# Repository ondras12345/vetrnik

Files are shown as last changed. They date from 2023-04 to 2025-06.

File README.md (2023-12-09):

# vetrnik
Power electronics for heating water using power generated by a small wind
turbine.

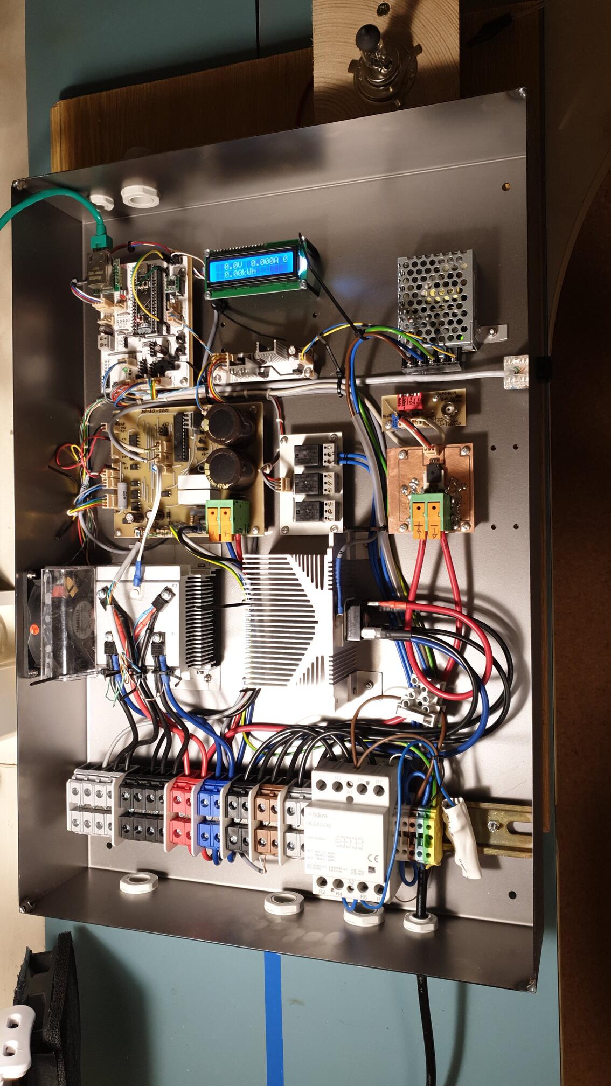
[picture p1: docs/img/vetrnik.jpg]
A photograph of the enclosure containing the wind turbine control electronics


## Features / design goals
- No battery.
- Maximum power point tracking.
- Power to resistive heating elements is AC to prevent electrolytic corrosion.
- MQTT telemetry.
- Home Assistant integration via MQTT.
- Energy meter.
- Calculates RPM from wind turbine AC output frequency.
- Survives full 50 V / 40 A during normal operation, as well as significantly
  higher open-circuit voltage.

The device offers a feature-rich command line interface:
```
vetrnik-control:$ help
---- Available commands ----

SPIflash: Issue commands to SPI flash
conf: Get or set configuration options.
control: Get or set params of control algorithm.
debug: Filter debug messages
dfu: Switch to DFU firmware download mode.
ds18b20: Print out DS18B20 sensor readings
free: Print out amount of free memory.
ifconfig: Print out networking information.
lisp: Process a line of Lisp
lisp_read: Execute Lisp from file
lisp_reset: Reinit Lisp interpreter
log: Print log / postmort
millis: Returns the number of milliseconds passed since the program started.
mqtt: Print out MQTT status.
onewirescan: Scan devices on onewire bus
ota: Switch to over-the-air firmware dl mode.
power: Print status of power PCB or set params.
pump: Control circulation pump.
reset: Reset the MCU.
rx: Print out RX_datapoints.
rx_raw: Toggle printing of messages from power board.
stats: Get stats (energy, ...)
tx: Set value of TX datapoint.
tx_raw: Transmit message to power board.
uptime: Returns the time passed since the program started.
ver: Print out version info.
watch: Run command every second.

vetrnik-control:$ stats
stats:
energy: 0.000 kWh

vetrnik-control:$ power
power board status:
retrieved_millis: 2274816315
valid: 1
time: 56810 s
mode: 2
duty: 0 (0-255)
OCP_max_duty: 255 (0-255)
RPM: 0 RPM
voltage: 0.0 V
current: 0.000 A
enabled.hardware: 1
enabled.software: 1
enabled.overall: 1
emergency: 0
temperature_heatsink: 16.3 'C
temperature_rectifier: 16.4 'C
fan: 0
error_count: 0
last5m: 0

vetrnik-control:$ ds18b20
This command does NOT request a new conversion.
[0] voda: 28.93 C
[1] : 0.00 C
[2] : 0.00 C
[3] : 0.00 C
[4] : 0.00 C
[5] : 0.00 C
[6] : 0.00 C
[7] : 0.00 C
[8] : 0.00 C
[9] : 0.00 C

vetrnik-control:$ SPIflash -h
Usage: SPIflash [erase_chip|ls | create name length erasable | rm name
   | dump name start | dumpchip start | erase filename | ed filename start]

vetrnik-control:$ SPIflash ls
Files:
address (HEX)	name	size (Bytes)
010000	settings	65536
020000	init.lisp	65536

vetrnik-control:$ lisp (= test (/ (+ 1 3) 2))
nil
Success: 1

vetrnik-control:$ lisp test
2
Success: 1

vetrnik-control:$ log
Usage: log (all|new)

vetrnik-control:$ log all
Printing whole log...
---
[      0] event: 0x0D log reinit
[      0] boot: 0x05 POWER-ON_RESET (POR) / POWER-DOWN_RESET (PDR)
[      0] event: 0x00 Eth begin
[      5] event: 0x01 Eth got IP
[      5] control strategy: old=control_shorted new=control_shorted
[      5] MQTT state: -1 DISCONNECTED
[     20] event: 0x03 MQTT connected
[     21] MQTT state: 0 CONNECTED
[   6315] control strategy: old=control_shorted new=control_lisp
[  82610] event: 0x10 DS18B20 error
[ 966931] MQTT state: -3 CONNECTION_LOST
[ 966932] event: 0x03 MQTT connected
[ 966932] MQTT state: 0 CONNECTED
[3386627] MQTT state: -2 CONNECT_FAILED
[3386810] event: 0x03 MQTT connected
[3386810] MQTT state: 0 CONNECTED
[3386870] event: 0x03 MQTT connected
[3387652] MQTT state: -3 CONNECTION_LOST
[3387652] event: 0x03 MQTT connected
[3387652] MQTT state: 0 CONNECTED
[3387712] event: 0x03 MQTT connected
[3387772] MQTT state: -3 CONNECTION_LOST
[3387772] event: 0x03 MQTT connected
[3387772] MQTT state: 0 CONNECTED
[3387814] control strategy: old=control_lisp new=control_shorted
[      0] boot: 0x04 SOFTWARE_RESET
[      0] event: 0x00 Eth begin
[      5] event: 0x01 Eth got IP
[      5] control strategy: old=control_shorted new=control_shorted
[      5] MQTT state: -1 DISCONNECTED
[     20] event: 0x03 MQTT connected
[     20] MQTT state: 0 CONNECTED
[     28] MQTT receive: length=1
[     29] MQTT receive: length=11
[     29] control strategy: old=control_shorted new=control_lisp
[ 118759] MQTT state: -3 CONNECTION_LOST
[ 118760] event: 0x03 MQTT connected
[ 118760] MQTT state: 0 CONNECTED
[ 721373] MQTT state: -3 CONNECTION_LOST
[ 721373] MQTT state: -2 CONNECT_FAILED
[ 721414] event: 0x03 MQTT connected
[ 721414] MQTT state: 0 CONNECTED
[ 982793] MQTT state: -3 CONNECTION_LOST
[ 982794] event: 0x03 MQTT connected
[ 982794] MQTT state: 0 CONNECTED
[ 983379] MQTT state: -3 CONNECTION_LOST
[ 983380] event: 0x03 MQTT connected
[ 983380] MQTT state: 0 CONNECTED
[2274043] MQTT receive: length=1
[2274062] MQTT receive: length=1
done

vetrnik-control:$
```

## Hardware details
See [`hardware/`](hardware/).

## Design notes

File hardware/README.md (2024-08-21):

# Vetrnik hardware
Block diagram:
```
            3 phase
+---------+ contactor +-----------+ DC +--------+ +-----------+ 1-phase +---------+
| Turbine +-+__/ __---+ rectifier +-+--+ ACS770 +-+ H-bridge  +---------+ heater  +
+---------+ |  ^      +-----------+ |  +----+---+ +-----------+ AC      +---------+
            |  |                    |       |          ^
            |  |             voltage|       |          |
            |  |                    |       | current  | duty
            |  |                    v       |          |
  frequency |  |      +-------------+-+     |          |
  (RPM)     |  +------+ vetrnik-power +<----+          |
            +-------->+               +----------------+
                      +-------+-------+
                              ^
                              | UART
                              v
                      +-------+-----------+
                      |  vetrnik-control  |
                      |                   +<----------> Ethernet
                      +-------------------+
```

The hardware consists of several PCBs in a custom-made enclosure. Most PCBs
are single-sided and designed to be milled out on a CNC.
- vetrnik-power
  - Controlled by an ATmega8 MCU.
  - Controls a FET H-bridge mounted on a heatsink.
  - Has isolated power supply, its GNDPWR is at wind turbine output potential.
  - Receives commands from vetrnik-control via optically isolated UART.
  - No remote firmware updates, no bootloader.
  - This PCB also contains analog comparator-based emergency stop circuitry
    that handles over-voltage condition even if the MCU is not working.
- vetrnik-control
  - Controlled by STM32F401.
  - Handles smart features (Ethernet, telnet, MQTT).
  - Implements LISP-like interpreted language that can be used to send
    commands to vetrnik-power. MPPT controller is implemented on this device
    in LISP.
  - Supports OTA firmware updates.
- vetrnik-current-sensor
  - A double-sided PCB with heavy copper. It passes all the current from the
    bridge rectifier through an ACS770-050U hall-effect current sensor.
- vetrnik-current-sensor-opamp
  - This PCB contains some additional signal-conditioning circuitry to improve
    current sensing precision and filter out noise.
- vetrnik-power-supply
  - A power supply board that converts 12 V from MeanWell power supply to
    various voltage levels needed by the device.
    The 3.3V voltage regulator is switch mode, 5V regulator is linear.
- vetrnik-relays
  - This is just a simple board with 3 relays that can be used to switch 230V
    devices like the coil of the contactor used to disconnect the wind turbine
    output, and a circulator pump.

## Wind turbine
- iSta breeze i-2000 Windsafe
- three phase
- 2 kW nominal power, 2.2 kW max
- 6 pole pairs --> 10 RPM / Hz

## Load
- 4x 600 W resistive heating element
- https://www.growzone.cz/48V-1200W-topna-patrona-G-6-4-palce-38x-197mm-d8275.htm

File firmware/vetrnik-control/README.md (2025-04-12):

# vetrnik-control
Firmware for STM32F4. Handles telemetry and remote control via MQTT,
MPPT controller, etc.

## Architecture
```text
        +-------+   +-------+     +----------+   cmnd_tx_raw
        | LISP  |   | MQTT  |     | CLI      +-----------------+
        +---+---+   +---+-+-+     +-----+--+-+                 |
            |           | |             |  | cmnd_tx           |
      +-----|-----------|-+-------------|--+                   |
RX_   |     |           |               |                      |
data  | +---+-----------+---------------+---------------+      |
points| |               wt_hal / hal.c                  |      |
_get()| +--------+----------------------+---------+-----+      |
  /   |          |                      |         |            |
TX_   | +--------+----------+     +-----+-----+   |            |
data  | | power_board       |     | control   |   |            |
points| +--------+----------+     +-----------+   |            |
_set()|==========|================================|============|===============
    +-+----------+--------+                       |            |
    | power_datapoints    |                       |            |
    +------------+--------+                       |            |
                 |                                |            |
        +--------+----+                   +-------+-----+      |     HARDWARE
        | uart_power  |                   | sensor_wind |      |      DRIVERS
        +--------+----+                   +-------+-----+      |
                 |                                |            |
                 +<-------------------------------|------------+
                 | UART                           |
=================|================================|============================
                 |                                |                 HARDWARE
    +------------+--------+       +---------------+-----+
    | vetrnik-power PCB   |       | wind sensor (RS485) |
    +---------------------+       +---------------------+
```

## Lisp-like REPL
A Lisp-like interpreted language called [fe](https://github.com/rxi/fe) is
included. It can be used by calling the `lisp` CLI command or via MQTT.

The intention is that the user can write a custom control algorithm and have
it run directly on the device without updating its firmware.

See [`lisp/spec.md`](lisp/spec.md).

### MISC Lisp code
Test OOM:
```lisp
(= a 0)
(while t
  (= l (cons a l))
  (= a (+ a 1))
)
```
On PC: a = 1852, does not get completely stuck (can still create new numeric
variables)
On STM (8*1024 bytes): a = 329

Patch for testing in lab without DS18B20 sensors:
```lisp
(= ds18 (fn () 23.4))
```

## Telnet
To connect with telnet on GNU/Linux, use this command:
```sh
# netcat - better
stty -icanon -echo && nc -NC -O 1 192.168.1.188 23

# telnet - sends garbage at startup
telnet 192.168.1.188 23  # specifying the port should disable negotiation
```

It is recommended to put the following configuration in your `~/.telnetrc` if
you want to use the `telnet` command:
```
# vetrnik-control
192.168.1.188
    mode character
    # TODO improve
```

## Build
Just run `make` in this directory. GNU/Linux OS with PlatformIO installed is
required.
Type `make help` for more info.

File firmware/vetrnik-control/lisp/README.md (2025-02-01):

# Lisp
This directory contains the lisp code for vetrnik-control.

Type `make` to compile `out.lisp`, which is the file to be written to the SPI
flash.

This directory also contains [documentation for the lisp
environment](spec.md) (automatically generated from `spec.yaml` by
`make`).

## Uploading
Simple:
```
# connect via telnet (do not use that nc trick, it does not work)
erase init.lisp
hexdump init.lisp 0
ed init.lisp 0
# paste out.lisp
.
reset
```

Advanced:
```
filltext init.lisp
# will print end address
ed init.lisp $end_addr+1
# paste out.lisp
.
reset
# (or lisp_reset & lisp_read with addr)
```

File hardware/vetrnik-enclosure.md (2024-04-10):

# Vetrnik enclosure
## Cable feed-throughs
- 230V IN: OD 7mm, GPA-M16
- wind turbine IN: EG-13.5GY (drill 20,4mm)
- heater OUT: EG-13.5GY (drill 20,4mm) + EG-13.5GY (90mm from left edge)
- ethernet UTP: EG-7BL (drill 12,5mm)
- USB-C: EG-13.5GY (drill 20,4mm) (combine with mechanical thermostat, temp sensors)
- temperature sensors: RJ45 KEJ-C5E-U-BK 20x15mm
- dump load?: EG-13.5GY (drill 20,4mm)
- 230V pump: GPA-M16 (50mm from right edge)

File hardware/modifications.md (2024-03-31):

- See `heater-elements.ipynb`.
- 2023-12-24 10:17 jsme zjistili, ze odesly Q2, Q4 v H-mustku (zkrat)
  - Q3 odpojen cerveny vodic
  - Q2 odpojen cerny vodic
  - melo by to fungovat jako half-bridge
  - Q2, Q4 piskala kontinuita cerny vodic proti modre svorkovnici
  - myslim, ze tranzistory odesly okolo 2023-12-22 22:00
    - Tocila se vrtule a ja se ji snazil rucne zastavit. Pri startu do male
      stridy se resetovala vykonova elektronika. Dal jsem vic (asi 50?),
      vrtule se zastavila.
    - Ale vubec to tim byt nemusi, protoze hned potom jsem navysil
      RL z 80 na 200?, takze proto od te doby tekly vetsi proudy.
  - Mohly umrit na prepeti (vrtule se volne tocila >1000 RPM >160V, v noci
    predtim dokonce nemerena (vypadlo 230V).
  - Nebo mohly umrit na to, ze byla spatne zapojena zatez (4 smycky
    paralelne), ale to bylo porad mnohem vic nez Rds on.

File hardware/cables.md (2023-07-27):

# Cables
## DS18B20 temperature sensors
- RJ45:

| pin | color | function | DS18B20 pin |
|:-----:|:---:|:---|:---:|
| 1 | orange/white  | | |
| 2 | orange | +5V | 3 |
| 3 | green/white | | |
| 4 | blue | 1-wire data | 2 |
| 5 | blue/white | GND | 1 |
| 6 | green | | |
| 7 | brown/white | | |
| 8 | brown | | |

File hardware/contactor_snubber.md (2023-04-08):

# Contactor RC snubber
Ethernet module would reset when contactor was operating (both on and off).
With a x100 oscilloscope probe, I was able to detect 1.5kV peak from one relay
contact to PE when the contactor was switching off. With the RC snubber in
parallel with relay contacts, the contactor would never switch off after being
operated once due to current flowing through the capacitor. RC snubber in
parallel with contactor's coil would reduce the peak voltage to <700V.
However, it wouldn't prevent the Ethernet module from resetting. I had to add
a 10nF capacitor to the module's RSTn pin for that.

There is some info about RC snubber desing in `contactor_snubber.m`.
However, I decided to use the generic laskakit.cz snubber (100 nF, 220 ohm and
a MOV). I'll likely need to put a fuse in series to protect from MOV failure.

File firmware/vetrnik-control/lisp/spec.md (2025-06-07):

# Language
See [fe language overview](https://github.com/rxi/fe/blob/master/doc/lang.md)
for more information about the language and built-in functions.

# Types
- number: a floating-point number
- string: a sequence of characters
- nil: always `nil`
- bool: either `nil` (false), or any other value (true)
- any: placeholder used in this document to indicate values of
  more than one type are acceptable.

# Categories
- LCD: functions that control the display
- callbacks: functions to be implemented by the user to respond to various events

# Custom functions
## `rem`
### Description
Perform the operation truncate on number and divisor and return the
remainder of the truncate operation.

https://stackoverflow.com/questions/5706398/how-to-get-the-modulus-in-lisp

### Signature
```lisp
(rem
    number
    divisor
)
```

### Arguments
- `number` \[number\]
- `divisor` \[number\]

### Return value
\[number\]: `(int)x % (int)y`

### Example
```lisp
(rem 3 2) ; 1
(rem -3 2) ; -1
```

## `round`
### Description
Return the closest integer to x, rounding to even when x is halfway between two integers.

### Signature
```lisp
(round
    x
)
```

### Arguments
- `x` \[number\]: number to round

### Return value
\[number\]

### Example
```lisp
(round 0.4999) ; 0
(round 0.5) ; 0
(round 0.5001) ; 1

(round 1.4999) ; 1
(round 1.5) ; 2
(round 1.5001) ; 2
```

## `map`
### Description
Linearly map a value from one range to another.

This could be easily implemented in Lisp, but a cfunc takes up less
memory.
Equivalent lisp implementation:
```lisp
(= map (fn (v fl fh tl th)
  (+ tl
     (/ (* (- v fl)
           (- th tl))
        (- fh fl)))))
```

### Signature
```lisp
(map
    value
    from_low
    from_high
    to_low
    to_high
)
```

### Arguments
- `value` \[number\]: the number to map
- `from_low` \[number\]: lower bound of `value`'s current range
- `from_high` \[number\]: upper bound of `value`'s current range
- `to_low` \[number\]: lower bound of `value`'s target range
- `to_high` \[number\]: upper bound of `value`'s target range

### Return value
\[number\]: `value` remapped to the target range

### Example
```lisp
(map 10 0 100 0 1) ; 0.1
(map 10 0 100 -1 0) ; -0.9
```

## `lim`
### Description
Limit a number to a range.

Equivalent lisp implementation:
```lisp
(= lim (fn (x l h)
  (if
    (< x l) l
    (< h x) h
    x)))
```

### Signature
```lisp
(lim
    x
    low
    high
)
```

### Arguments
- `x` \[number\]: value to be processed
- `low` \[number\]: lower bound for the value's range
- `high` \[number\]: upper bound for the value's range

### Return value
\[number\]
## `pow`
### Description
Compute x raised to the power of y.

### Signature
```lisp
(pow
    x
    y
)
```

### Arguments
- `x` \[number\]
- `y` \[number\]

### Return value
\[number\]
## `pwrg`
### Description
Get a value from the power board state object. Numerical values (in SI units without metric prefix) are returned.

### Signature
```lisp
(pwrg
    name
    [relay_nr]
)
```

### Arguments
- `name` \[string\]
    - `"valid"`
    - `"time"`
    - `"mode"`
    - `"duty"`
    - `"OCP_max_duty"`
    - `"RPM"`
    - `"voltage"`
    - `"current"`
    - `"hw_enable"`
    - `"sw_enable"`
    - `"enabled"`
    - `"emergency"`
- `relay_nr` \[number\]: relay number (starting from 1); only used if name == "REL"

### Return value
\[any\]
## `pwrs`
### Description
Set parameters on the power board.

Variables are added for the constants from `power_board_mode_t` enum.
They are prefixed with `pwr_`, e.g. `pwr_start`.

### Signature
```lisp
(pwrs
    name
    value
    ...
)
```

### Arguments
- `name` \[string\]
    - `"duty"`
    - `"mode"`
    - `"REL"`
    - `"sw_enable"`
- `value` \[any\]: Desired value (expected type depends on 'name')

### Return value
\[nil\]
## `lcdc`
Category: LCD

### Description
Set LCD cursor position to specified column.

### Signature
```lisp
(lcdc
    column
)
```

### Arguments
- `column` \[number\]

### Return value
\[nil\]
## `lcdw`
Category: LCD

### Description
Write LCD buffer to specified line (row).

### Signature
```lisp
(lcdw
    row
)
```

### Arguments
- `row` \[number\]

### Return value
\[nil\]
## `lcds`
Category: LCD

### Description
Print a string to the LCD buffer.

### Signature
```lisp
(lcds
    str
)
```

### Arguments
- `str` \[string\]

### Return value
\[nil\]
## `lcdn`
Category: LCD

### Description
Print a number to the LCD buffer.

### Signature
```lisp
(lcdn
    number
    align
    precision
)
```

### Arguments
- `number` \[number\]: number to print
- `align` \[number\]: (integer) TODO
- `precision` \[any\]: (integer) number of decimal places (TODO verify)

### Return value
\[nil\]
## `lcdb`
Category: LCD

### Description
Get or set LCD backlight status.

### Signature
```lisp
(lcdb
    [state]
)
```

### Arguments
- `state` \[bool\]: Desired backlight status

### Return value
\[bool\]: LCD backlight status
## `stats`
### Description
Get a value from the stats struct.

### Signature
```lisp
(stats
    name
)
```

### Arguments
- `name` \[string\]
    - `"energy"`

### Return value
\[number\]: value
## `ctrlg`
### Description
Get a value from the control subsystem.

### Signature
```lisp
(ctrlg
    name
)
```

### Arguments
- `name` \[string\]
    - `"strategy"`
    - `"contactor"`
    - `"vwind"`

### Return value
\[any\]
## `ctrls`
### Description
Set a value in the control subsystem.

### Signature
```lisp
(ctrls
    name
    value
)
```

### Arguments
- `name` \[string\]
    - `"strategy"`
    - `"contactor"`
- `value` \[any\]: Desired value (expected type depends on 'name')

### Return value
\[nil\]
## `out`
### Description
Get or set state of digital outputs (LEDs and relays) on the control board.

### Signature
```lisp
(out
    out_id
    [state]
)
```

### Arguments
- `out_id` \[string\]
    - `"LED_BLUE"`
    - `"LED_RED"`
    - `"PUMP"`
    - `"REL2"`
- `state` \[bool\]: desired state

### Return value
\[bool\]: state of the digital output
## `ds18`
### Description
Read temperature from DS18B20 sensors.

### Signature
```lisp
(ds18
    sensor_number
)
```

### Arguments
- `sensor_number` \[number\]

### Return value
\[number\]: temperature in degrees C. nil is returned if sensor is broken.
## `ctrl`
Category: callbacks

### Description
If set up for `LISP` control strategy, the device will call this function
each time a new state object is received.
This function is empty by default, the user is expected to overwrite it
with their own implementation.

### Signature
```lisp
(ctrl
)
```

### Arguments

### Return value
\[nil\]

### Example
```lisp
;;; A simple "blink" control function:
(= dl 50) ; off state duty
(= dh 200) ; on state duty
(= p 5) ; period in seconds
(= pt 0) ; prev time
(= ctrl (fn ()
  ; t is used for "true", do not overwrite - named ti instead
  (let ti (pwrg "time"))
  ; max time is 65535 (see power report()), so no problem with rem
  (if (and (is (rem ti p) 0) (not (is ti pt)))
    (do
      (= pt ti)
      (pwrs "duty" (if (<= (pwrg "duty") dl) dh dl))
    )
  )
))

;;; Simple RPM threshold-based control:
(= ctrl (fn ()
  (let r (pwrg "RPM")) ; current RPM
  (pwrs "duty"
    (if
      ; pretty much random values
      (< r 10) 0
      (< r 15) 10
      (< r 20) 20
      (< r 30) 40
      (< r 60) 100
      255
    )
  )
))
```

## `disp`
Category: callbacks

### Description
The `disp` function is executed every 0.5 s. It is meant to be used to
control the display.
This function is empty by default, the user is expected to overwrite it
with their own implementation.

### Signature
```lisp
(disp
)
```

### Arguments

### Return value
\[nil\]
## `btn1_short`
Category: callbacks

### Description
Called when button 1 is released after a short press.

### Signature
```lisp
(btn1_short
)
```

### Arguments

### Return value
\[nil\]
## `btn1_long`
Category: callbacks

### Description
Called when button 1 is released after a long press.

### Signature
```lisp
(btn1_long
)
```

### Arguments

### Return value
\[nil\]
## `btn2_short`
Category: callbacks

### Description
Called when button 2 is released after a short press.

### Signature
```lisp
(btn2_short
)
```

### Arguments

### Return value
\[nil\]
## `btn2_long`
Category: callbacks

### Description
Called when button 2 is released after a long press.

### Signature
```lisp
(btn2_long
)
```

### Arguments

### Return value
\[nil\]

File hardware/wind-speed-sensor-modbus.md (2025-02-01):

# Wind speed sensor modbus
- RS-FSJT-N01

## Initial testing
- 12 V power brown +, black -
- yellow (green) RS-485 A, blue: RS-485 B
- PL2303-485 USB converter (PL-2303HX + MAX485ESA)

```console
$ sudo apt install mbpoll

$ mbpoll -m rtu -a 1 -t 3 -r 1 -c 1 -l 500 -b 4800 /dev/ttyUSB0
# does not work

# debug:
$ mbpoll -v -m rtu -a 1 -t 3 -r 1 -c 1 -l 500 -b 4800 /dev/ttyUSB0
debug enabled
Set mode=rtu
iGetIntList(1)
Integer found: 1
iCount=1
Set function=3
Set start reference=1
Set number of values=1
Set poll rate=500
Set rtu baudrate=4800
Set device=/dev/ttyUSB0
mbpoll 1.0-0 - FieldTalk(tm) Modbus(R) Master Simulator
Copyright © 2015-2019 Pascal JEAN, https://github.com/epsilonrt/mbpoll
This program comes with ABSOLUTELY NO WARRANTY.
This is free software, and you are welcome to redistribute it
under certain conditions; type 'mbpoll -w' for details.

Opening /dev/ttyUSB0 at 4800 bauds (E, 8, 1)
Set response timeout to 1 sec, 0 us
Protocol configuration: Modbus RTU
Slave configuration...: address = [1]
                        start reference = 1, count = 1
Communication.........: /dev/ttyUSB0,       4800-8E1 
                        t/o 1.00 s, poll rate 500 ms
Data type.............: 16-bit register, input register table

-- Polling slave 1... Ctrl-C to stop)
[01][04][00][00][00][01][31][CA]
Waiting for a confirmation...
<01><00><00><00><00>
ERROR CRC received 0x0 != CRC calculated 0x2000
Read input register failed: Invalid CRC
-- Polling slave 1... Ctrl-C to stop)
[01][04][00][00][00][01][31][CA]
Waiting for a confirmation...
<01><00><00><00><00>
ERROR CRC received 0x0 != CRC calculated 0x2000
Read input register failed: Invalid CRC
-- Polling slave 1... Ctrl-C to stop)
[01][04][00][00][00][01][31][CA]
Waiting for a confirmation...
<01><00><00><00><FE>
ERROR CRC received 0xFE != CRC calculated 0x2000
Read input register failed: Invalid CRC
-- Polling slave 1... Ctrl-C to stop)
[01][04][00][00][00][01][31][CA]
Waiting for a confirmation...
<01><00><00><00><FE>
ERROR CRC received 0xFE != CRC calculated 0x2000
Read input register failed: Invalid CRC
```

According to the manual, only modbus function code 0x03 (read register data)
is supported.

```console
$ mbpoll -v -m rtu -a 1 -t 4 -r 1 -c 1 -l 500 -b 4800 /dev/ttyUSB0
debug enabled
Set mode=rtu
iGetIntList(1)
Integer found: 1
iCount=1
Set function=4
Set start reference=1
Set number of values=1
Set poll rate=500
Set rtu baudrate=4800
Set device=/dev/ttyUSB0
mbpoll 1.0-0 - FieldTalk(tm) Modbus(R) Master Simulator
Copyright © 2015-2019 Pascal JEAN, https://github.com/epsilonrt/mbpoll
This program comes with ABSOLUTELY NO WARRANTY.
This is free software, and you are welcome to redistribute it
under certain conditions; type 'mbpoll -w' for details.

Opening /dev/ttyUSB0 at 4800 bauds (E, 8, 1)
Set response timeout to 1 sec, 0 us
Protocol configuration: Modbus RTU
Slave configuration...: address = [1]
                        start reference = 1, count = 1
Communication.........: /dev/ttyUSB0,       4800-8E1 
                        t/o 1.00 s, poll rate 500 ms
Data type.............: 16-bit register, output (holding) register table

-- Polling slave 1... Ctrl-C to stop)
[01][03][00][00][00][01][84][0A]
Waiting for a confirmation...
<01><00><00><B8><00>
ERROR CRC received 0xB800 != CRC calculated 0x2000
Read output (holding) register failed: Invalid CRC
-- Polling slave 1... Ctrl-C to stop)
[01][03][00][00][00][01][84][0A]
Waiting for a confirmation...
<01><00><00><00><00>
ERROR CRC received 0x0 != CRC calculated 0x2000
Read output (holding) register failed: Invalid CRC
-- Polling slave 1... Ctrl-C to stop)
[01][03][00][00][00][01][84][0A]
Waiting for a confirmation...
<01><00><00><00><00>
ERROR CRC received 0x0 != CRC calculated 0x2000
Read output (holding) register failed: Invalid CRC
^C--- /dev/ttyUSB0 poll statistics ---
3 frames transmitted, 0 received, 3 errors, 100.0% frame loss

everything was closed.
Have a nice day !
```

Now the query matches the manual, but there still is no response.

Connected grounds together.

I can see responses on the oscilloscope, but mbpoll still complains:
```console
$ mbpoll -v -m rtu -a 1 -t 4 -r 1 -c 1 -l 500 -b 4800 /dev/ttyUSB0
debug enabled
Set mode=rtu
iGetIntList(1)
Integer found: 1
iCount=1
Set function=4
Set start reference=1
Set number of values=1
Set poll rate=500
Set rtu baudrate=4800
Set device=/dev/ttyUSB0
mbpoll 1.0-0 - FieldTalk(tm) Modbus(R) Master Simulator
Copyright © 2015-2019 Pascal JEAN, https://github.com/epsilonrt/mbpoll
This program comes with ABSOLUTELY NO WARRANTY.
This is free software, and you are welcome to redistribute it
under certain conditions; type 'mbpoll -w' for details.

Opening /dev/ttyUSB0 at 4800 bauds (E, 8, 1)
Set response timeout to 1 sec, 0 us
Protocol configuration: Modbus RTU
Slave configuration...: address = [1]
                        start reference = 1, count = 1
Communication.........: /dev/ttyUSB0,       4800-8E1 
                        t/o 1.00 s, poll rate 500 ms
Data type.............: 16-bit register, output (holding) register table

-- Polling slave 1... Ctrl-C to stop)
[01][03][00][00][00][01][84][0A]
Waiting for a confirmation...
<01><00><00><00><00>
ERROR CRC received 0x0 != CRC calculated 0x2000
Read output (holding) register failed: Invalid CRC
-- Polling slave 1... Ctrl-C to stop)
[01][03][00][00][00][01][84][0A]
Waiting for a confirmation...
<01><00><00><00><00>
ERROR CRC received 0x0 != CRC calculated 0x2000
Read output (holding) register failed: Invalid CRC
-- Polling slave 1... Ctrl-C to stop)
[01][03][00][00][00][01][84][0A]
Waiting for a confirmation...
<01><00><00><00><00>
ERROR CRC received 0x0 != CRC calculated 0x2000
Read output (holding) register failed: Invalid CRC
^C--- /dev/ttyUSB0 poll statistics ---
3 frames transmitted, 0 received, 3 errors, 100.0% frame loss

everything was closed.
Have a nice day !
```

Parity was not set properly.
```console
$ mbpoll -m rtu -a 1 -t 4 -r 1 -c 1 -l 500 -b 4800 -P none /dev/ttyUSB0
mbpoll 1.0-0 - FieldTalk(tm) Modbus(R) Master Simulator
Copyright © 2015-2019 Pascal JEAN, https://github.com/epsilonrt/mbpoll
This program comes with ABSOLUTELY NO WARRANTY.
This is free software, and you are welcome to redistribute it
under certain conditions; type 'mbpoll -w' for details.

Protocol configuration: Modbus RTU
Slave configuration...: address = [1]
                        start reference = 1, count = 1
Communication.........: /dev/ttyUSB0,       4800-8N1 
                        t/o 1.00 s, poll rate 500 ms
Data type.............: 16-bit register, output (holding) register table

-- Polling slave 1... Ctrl-C to stop)
[1]: 	0
-- Polling slave 1... Ctrl-C to stop)
[1]: 	0
-- Polling slave 1... Ctrl-C to stop)
[1]: 	0
-- Polling slave 1... Ctrl-C to stop)
[1]: 	0
-- Polling slave 1... Ctrl-C to stop)
[1]: 	0
-- Polling slave 1... Ctrl-C to stop)
[1]: 	0
-- Polling slave 1... Ctrl-C to stop)
[1]: 	0
-- Polling slave 1... Ctrl-C to stop)
[1]: 	0
-- Polling slave 1... Ctrl-C to stop)
[1]: 	11
-- Polling slave 1... Ctrl-C to stop)
[1]: 	14
-- Polling slave 1... Ctrl-C to stop)
[1]: 	14
-- Polling slave 1... Ctrl-C to stop)
[1]: 	11
-- Polling slave 1... Ctrl-C to stop)
[1]: 	11
-- Polling slave 1... Ctrl-C to stop)
[1]: 	8
-- Polling slave 1... Ctrl-C to stop)
[1]: 	8
-- Polling slave 1... Ctrl-C to stop)
[1]: 	6
-- Polling slave 1... Ctrl-C to stop)
[1]: 	6
-- Polling slave 1... Ctrl-C to stop)
[1]: 	4
-- Polling slave 1... Ctrl-C to stop)
[1]: 	4
-- Polling slave 1... Ctrl-C to stop)
[1]: 	2
-- Polling slave 1... Ctrl-C to stop)
[1]: 	2
-- Polling slave 1... Ctrl-C to stop)
[1]: 	2
-- Polling slave 1... Ctrl-C to stop)
[1]: 	1
-- Polling slave 1... Ctrl-C to stop)
[1]: 	1
-- Polling slave 1... Ctrl-C to stop)
[1]: 	1
-- Polling slave 1... Ctrl-C to stop)
[1]: 	1
-- Polling slave 1... Ctrl-C to stop)
[1]: 	0
-- Polling slave 1... Ctrl-C to stop)
[1]: 	0
-- Polling slave 1... Ctrl-C to stop)
[1]: 	0
^C--- /dev/ttyUSB0 poll statistics ---
29 frames transmitted, 29 received, 0 errors, 0.0% frame loss

everything was closed.
Have a nice day !
```

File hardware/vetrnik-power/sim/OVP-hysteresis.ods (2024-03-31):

R1 | R2 | Vin | Vout |  |  | Vcc | R25 | R26 | R29 | R30 | Vh | Vl | Vhh nominal | 1,1*Vh | Vhh +10% | Vhh – 5% | Vll – 5%
1,00E+05 | 3,30E+03 | 178,5 | 5,702 |  | puvodni | 12 | 47,00E+03 | 22,00E+03 | 47,00E+03 | 3,30E+03 | 5,702 | 2,901 | 178,500 | 6,273 | 196,3 | 169,6 | 86,3
1,00E+05 | 3,30E+03 | 90,8 | 2,901 |  |  | 12 | 68,00E+03 | 18,00E+03 | 100,00E+03 | 3,30E+03 | 3,661 | 2,199 | 114,588 | 4,027 | 126,0 | 108,9 | 65,4
1,00E+05 | 3,30E+03 | 128 | 4,089 | x |  | 12 | 47,00E+03 | 22,00E+03 | 220,00E+03 | 3,30E+03 | 4,340 | 3,582 | 135,859 | 4,774 | 149,4 | 129,1 | 106,5
1,00E+05 | 3,30E+03 | 100 | 3,195 | x |  | 12 | 13,90E+03 | 5,60E+03 | 47,00E+03 | 3,30E+03 | 4,075 | 3,176 | 127,562 | 4,483 | 140,3 | 121,2 | 94,5
1,00E+05 | 3,30E+03 | 80 | 2,556 | x |  | 12 | 61,00E+03 | 19,80E+03 | 100,00E+03 | 3,30E+03 | 4,086 | 2,558 | 127,898 | 4,494 | 140,7 | 121,5 | 76,1
1,00E+05 | 3,30E+03 | 109 | 3,482 |  |  | 12 | 68,00E+03 | 22,00E+03 | 120,00E+03 | 3,30E+03 | 4,010 | 2,576 | 125,538 | 4,411 | 138,1 | 119,3 | 76,6
1,00E+05 | 3,30E+03 | 56 | 1,789 |  |  | 12 | 61,00E+03 | 17,00E+03 | 100,00E+03 | 3,30E+03 | 3,685 | 2,308 | 115,367 | 4,054 | 126,9 | 109,6 | 68,6
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

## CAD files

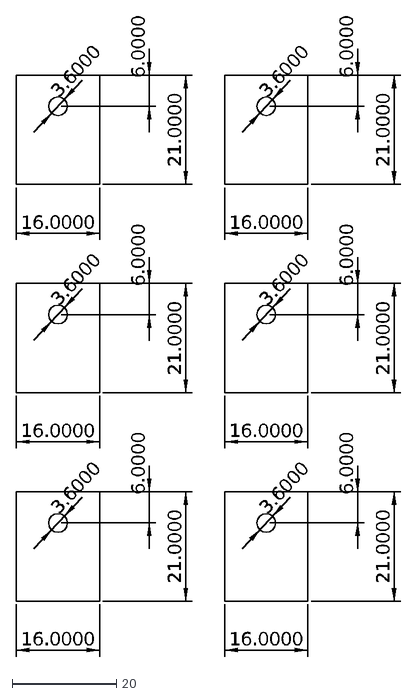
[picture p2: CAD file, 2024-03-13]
hardware/TO-247-scale.dxf
6.0000
21.0000
16.0000
3.6000

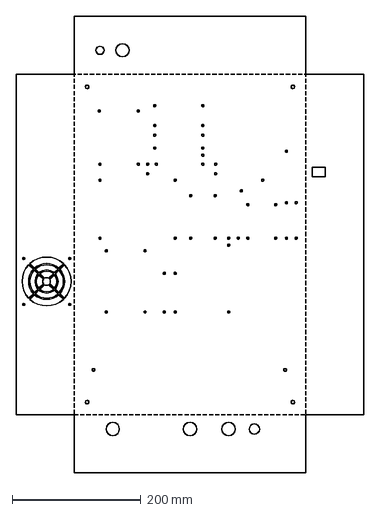
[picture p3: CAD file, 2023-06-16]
hardware/vetrnik-enclosure.dxf
540.0 x 710.0 mm

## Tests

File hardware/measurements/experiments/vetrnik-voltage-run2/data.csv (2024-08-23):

datetime | voltage_set | voltage_get1 | voltage_dmm1 | time1 | voltage_vetrnik1 | voltage_get2 | voltage_dmm2 | time2 | voltage_vetrnik2 | voltage_get3 | voltage_dmm3 | time3 | voltage_vetrnik3 | voltage_dmm1_V | voltage_dmm2_V | voltage_dmm3_V
2024-07-01 22:11:10.541995 | 2 | 2 | 02.342e00 V DC | 1354 | 2.1 | 2 | 02.369e00 V DC | 1355 | 2.1 | 2 | 02.383e00 V DC | 1357 | 2.1 | 2.342 | 2.369 | 2.383
2024-07-01 22:11:15.180022 | 3 | 3 | 03.930e00 V DC | 1359 | 3.6 | 3 | 03.957e00 V DC | 1360 | 3.8 | 3 | 03.967e00 V DC | 1361 | 3.8 | 3.93 | 3.957 | 3.967
2024-07-01 22:11:19.769974 | 5 | 5 | 07.140e00 V DC | 1363 | 6.8 | 5 | 07.156e00 V DC | 1365 | 7.0 | 5 | 07.158e00 V DC | 1366 | 7.0 | 7.14 | 7.156 | 7.158
2024-07-01 22:11:24.360379 | 10 | 10 | 014.39e00 V DC | 1368 | 14.2 | 11 | 014.39e00 V DC | 1369 | 14.2 | 11 | 014.40e00 V DC | 1370 | 14.2 | 14.39 | 14.39 | 14.4
2024-07-01 22:11:28.949898 | 15 | 16 | 022.47e00 V DC | 1373 | 22.2 | 16 | 022.50e00 V DC | 1374 | 22.2 | 16 | 022.51e00 V DC | 1375 | 22.4 | 22.47 | 22.5 | 22.51
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

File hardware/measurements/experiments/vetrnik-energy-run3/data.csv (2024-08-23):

datetime | time | energy_Ws_vetrnik | voltage_vetrnik | current_vetrnik | power_vetrnik | voltage_dmm | current_dmm | voltage_dmm_V | current_dmm_A | duration | power_dmm | energy_Ws_dmm
2024-07-04 16:54:33.008086 | 1192 | 0.0 | 10.3 | 0.0 | 0.0 | OVLOAD V DC | 00.000e00 A DC |  | 0.0 | 0.997626
2024-07-04 16:54:34.005712 | 1193 | 0.0 | 10.5 | 0.0 | 0.0 | OVLOAD V DC | 00.000e00 A DC |  | 0.0 | 0.999737
2024-07-04 16:54:35.005449 | 1194 | 0.0 | 10.5 | 0.0 | 0.0 | OVLOAD V DC | 00.000e00 A DC |  | 0.0 | 0.998184
2024-07-04 16:54:36.003633 | 1195 | 0.0 | 10.5 | 0.0 | 0.0 | 10.713e00 V DC | 00.000e00 A DC | 10.713 | 0.0 | 0.999894 | 0.0 | 0.0
2024-07-04 16:54:37.003527 | 1196 | 0.0 | 10.5 | 0.0 | 0.0 | 10.665e00 V DC | 00.000e00 A DC | 10.665 | 0.0 | 1.000543 | 0.0 | 0.0
2024-07-04 16:54:38.004070 | 1197 | 0.0 | 10.5 | 0.0 | 0.0 | 10.665e00 V DC | 00.000e00 A DC | 10.665 | 0.0 | 0.999808 | 0.0 | 0.0
2024-07-04 16:54:39.003878 | 1198 | 0.0 | 10.5 | 0.0 | 0.0 | 10.665e00 V DC | 00.000e00 A DC | 10.665 | 0.0 | 1.000897 | 0.0 | 0.0
2024-07-04 16:54:40.004775 | 1199 | 0.0 | 10.5 | 0.0 | 0.0 | 10.665e00 V DC | 00.000e00 A DC | 10.665 | 0.0 | 1.002683 | 0.0 | 0.0
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

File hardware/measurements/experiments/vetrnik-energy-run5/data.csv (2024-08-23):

datetime | time | energy_Ws_vetrnik | voltage_vetrnik | current_vetrnik | power_vetrnik | voltage_dmm | current_dmm | voltage_dmm_V | current_dmm_A | duration | power_dmm | energy_Ws_dmm
2024-07-04 17:24:34.873608 | 2994 | 4615.7 | 9.9 | 0.041 | 0.4 | OVLOAD V DC | 00.071e00 A DC |  | 0.071 | 1.12994
2024-07-04 17:24:36.003548 | 2995 | 4616.2 | 10.0 | 0.041 | 0.4 | OVLOAD V DC | 00.074e00 A DC |  | 0.074 | 1.000005
2024-07-04 17:24:37.003553 | 2996 | 4616.5 | 10.0 | 0.041 | 0.4 | OVLOAD V DC | 00.074e00 A DC |  | 0.074 | 1.002061
2024-07-04 17:24:38.005614 | 2997 | 4616.9 | 10.0 | 0.041 | 0.4 | 10.139e00 V DC | 00.074e00 A DC | 10.139 | 0.074 | 1.001461 | 0.7502859999999999 | 0.7513821678459999
2024-07-04 17:24:39.007075 | 2998 | 4618.8 | 9.9 | 0.205 | 2.0 | 10.270e00 V DC | 00.376e00 A DC | 10.27 | 0.376 | 1.000302 | 3.86152 | 4.614068346886
2024-07-04 17:24:40.007377 | 2999 | 4619.9 | 10.0 | 0.041 | 0.4 | 10.270e00 V DC | 00.076e00 A DC | 10.27 | 0.076 | 0.996426 | 0.78052 | 5.391798768406001
2024-07-04 17:24:41.003803 | 3000 | 4620.1 | 10.0 | 0.0 | 0.0 | 10.201e00 V DC | 00.057e00 A DC | 10.201 | 0.057 | 0.99991 | 0.581457 | 5.973203437276001
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

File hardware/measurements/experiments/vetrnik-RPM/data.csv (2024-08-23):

datetime | amplitude | frequency | RPM1 | RPM2 | RPM3 | RPM4 | RPM5
2024-06-30 22:03:08.742834 | 4.5 | 1.0 | 13 | 9 | 9 | 9 | 9
2024-06-30 22:03:14.809333 | 4.5 | 2.0 | 33 | 33 | 19 | 19 | 19
2024-06-30 22:03:20.676530 | 4.5 | 4.0 | 43 | 39 | 39 | 39 | 39
2024-06-30 22:03:26.537270 | 4.5 | 6.0 | 59 | 59 | 59 | 59 | 59
2024-06-30 22:03:32.405925 | 4.5 | 10.0 | 99 | 99 | 99 | 99 | 99
2024-06-30 22:03:38.273071 | 4.5 | 12.0 | 119 | 119 | 119 | 119 | 119
2024-06-30 22:03:44.136235 | 4.5 | 15.0 | 149 | 149 | 149 | 149 | 149
2024-06-30 22:03:49.991906 | 4.5 | 19.0 | 189 | 189 | 189 | 189 | 189
2024-06-30 22:03:55.856881 | 4.5 | 23.0 | 172 | 229 | 200 | 229 | 200
2024-06-30 22:04:01.712002 | 4.5 | 28.0 | 0 | 0 | 0 | 0 | 0
2024-06-30 22:04:07.582373 | 4.5 | 35.0 | 0 | 0 | 0 | 0 | 0
2024-06-30 22:04:13.456064 | 4.5 | 43.0 | 0 | 0 | 0 | 0 | 0
2024-06-30 22:04:19.330581 | 4.5 | 53.0 | 0 | 0 | 0 | 0 | 0
2024-06-30 22:04:25.204625 | 4.5 | 65.0 | 0 | 0 | 0 | 0 | 0
2024-06-30 22:04:31.074336 | 4.5 | 80.0 | 0 | 0 | 0 | 0 | 0
2024-06-30 22:04:36.941706 | 4.5 | 84.0 | 0 | 0 | 0 | 0 | 0
2024-06-30 22:04:42.808656 | 4.5 | 88.0 | 0 | 0 | 0 | 0 | 0
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

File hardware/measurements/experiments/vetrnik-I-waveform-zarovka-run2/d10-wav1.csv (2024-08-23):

time [s] | CHANNEL1 [V]
-0.0025 | 0.22499942399999995
-0.0024975 | 0.22499942399999995
-0.0024950000000000003 | 0.22499942399999995
-0.0024925 | 0.21874941439999995
-0.00249 | 0.20624939519999996
-0.0024875 | 0.22499942399999995
-0.0024850000000000002 | 0.21874941439999995
-0.0024825 | 0.21249940479999996
-0.00248 | 0.21874941439999995
-0.0024775 | 0.21874941439999995
-0.002475 | 0.21874941439999995
-0.0024725 | 0.21249940479999996
-0.00247 | 0.21249940479999996
-0.0024675 | 0.21249940479999996
-0.002465 | 0.21249940479999996
-0.0024625 | 0.21249940479999996
-0.00246 | 0.20624939519999996
-0.0024575 | 0.21249940479999996
-0.002455 | 0.21249940479999996
-0.0024525000000000003 | 0.20624939519999996
-0.00245 | 0.21249940479999996
-0.0024475 | 0.20624939519999996
-0.002445 | 0.21249940479999996
-0.0024425000000000002 | 0.21874941439999995
-0.00244 | 0.21249940479999996
-0.0024375 | 0.21874941439999995
-0.002435 | 0.21249940479999996
-0.0024325 | 0.21249940479999996
-0.00243 | 0.21249940479999996
-0.0024275 | 0.19999938559999997
-0.002425 | 0.21874941439999995
-0.0024225 | 0.20624939519999996
-0.00242 | 0.21249940479999996
-0.0024175 | 0.21249940479999996
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

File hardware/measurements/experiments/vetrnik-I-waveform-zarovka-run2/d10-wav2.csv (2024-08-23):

time [s] | CHANNEL1 [V]
-0.0025 | 0.23124943359999994
-0.0024975 | 0.23124943359999994
-0.0024950000000000003 | 0.21249940479999996
-0.0024925 | 0.22499942399999995
-0.00249 | 0.20624939519999996
-0.0024875 | 0.22499942399999995
-0.0024850000000000002 | 0.21249940479999996
-0.0024825 | 0.21249940479999996
-0.00248 | 0.21874941439999995
-0.0024775 | 0.21874941439999995
-0.002475 | 0.21874941439999995
-0.0024725 | 0.21874941439999995
-0.00247 | 0.21874941439999995
-0.0024675 | 0.21249940479999996
-0.002465 | 0.20624939519999996
-0.0024625 | 0.21874941439999995
-0.00246 | 0.21249940479999996
-0.0024575 | 0.21874941439999995
-0.002455 | 0.21249940479999996
-0.0024525000000000003 | 0.20624939519999996
-0.00245 | 0.20624939519999996
-0.0024475 | 0.21249940479999996
-0.002445 | 0.21249940479999996
-0.0024425000000000002 | 0.20624939519999996
-0.00244 | 0.20624939519999996
-0.0024375 | 0.21874941439999995
-0.002435 | 0.21874941439999995
-0.0024325 | 0.20624939519999996
-0.00243 | 0.21874941439999995
-0.0024275 | 0.21249940479999996
-0.002425 | 0.21249940479999996
-0.0024225 | 0.20624939519999996
-0.00242 | 0.21249940479999996
-0.0024175 | 0.20624939519999996
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

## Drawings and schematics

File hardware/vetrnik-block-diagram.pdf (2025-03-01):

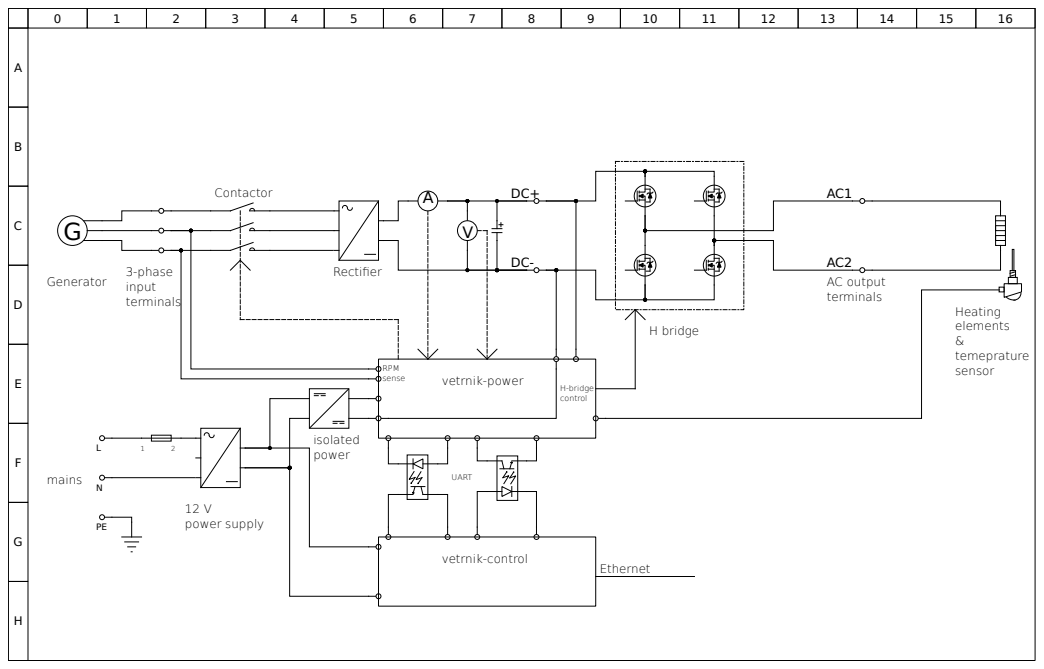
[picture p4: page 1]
isolated power; AC output terminals; Ethernet; Rectifier; Generator; vetrnik-power; Heating elements & temeprature sensor; 3-phase input terminals; Contactor; H bridge; RPM sense; H-bridge control; vetrnik-control; 12 V power supply; mains; UART

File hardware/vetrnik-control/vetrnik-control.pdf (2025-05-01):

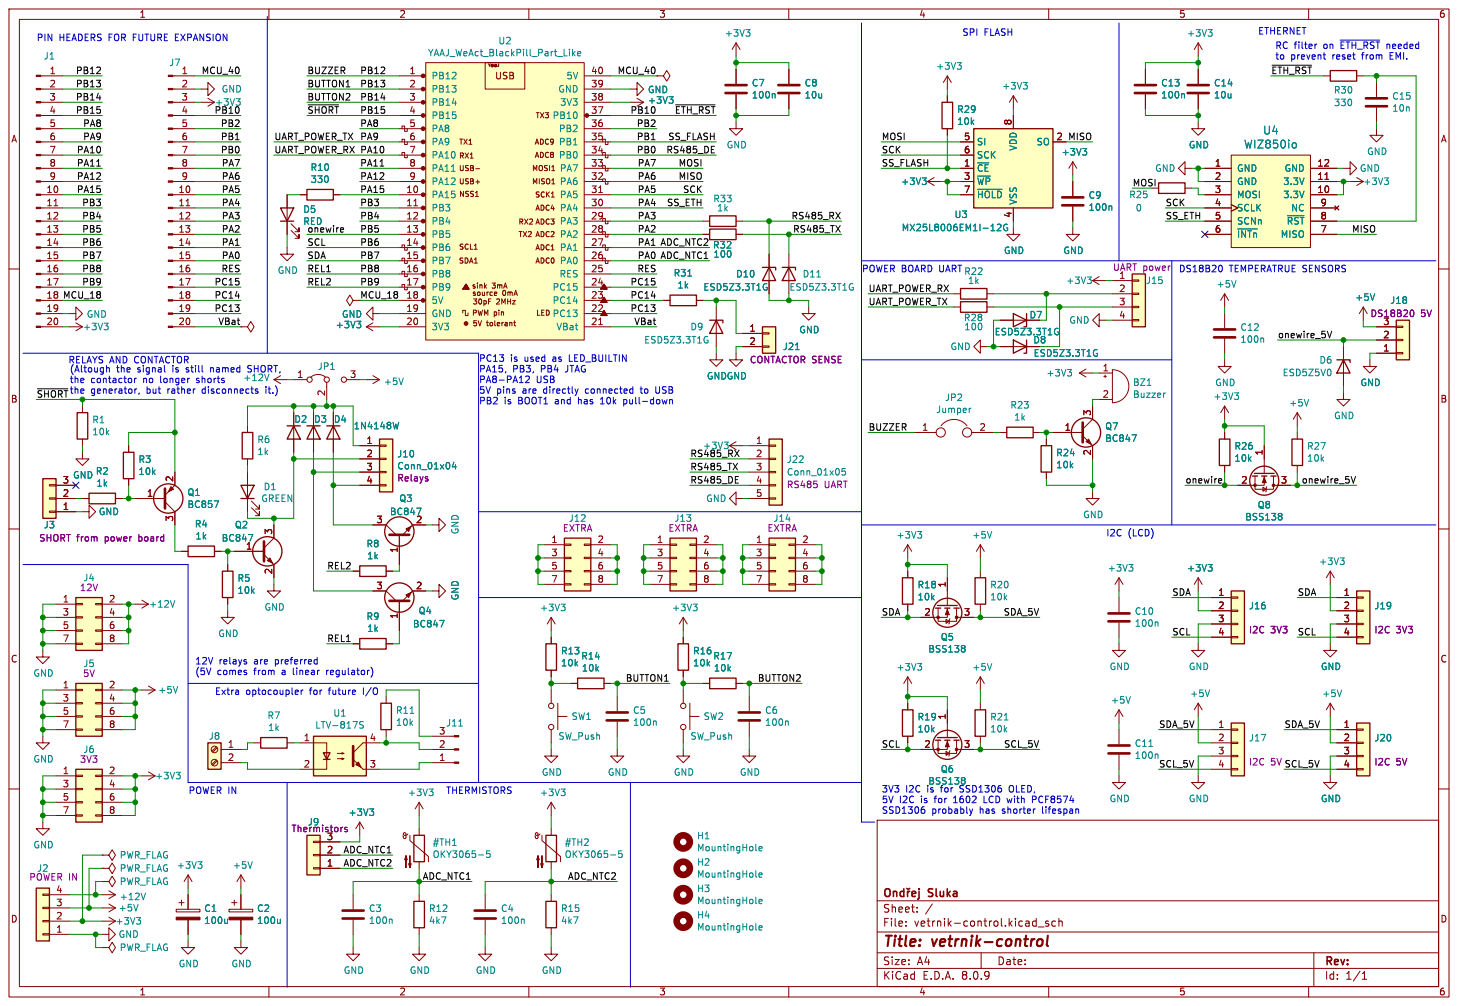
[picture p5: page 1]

ETHERNET RC filter on ~{ETH_RST}needed

4 SI 5 SCK 6 ~{HOLD} 7 VDD
100n +3V3 D7 ESD5Z3.3T1G

PC13 is used as LED_BUILTIN
PA15, PB3, PB4 JTAG
PB2 is BOOT1 and has 10k pull-down

Id: 1/1 Title: vetrnik-control File: vetrnik-control.kicad_sch Sheet: / þÿOndYej Sluka R2
1kGND

H1 MountingHole H2 MountingHole H3 MountingHole H4 MountingHole

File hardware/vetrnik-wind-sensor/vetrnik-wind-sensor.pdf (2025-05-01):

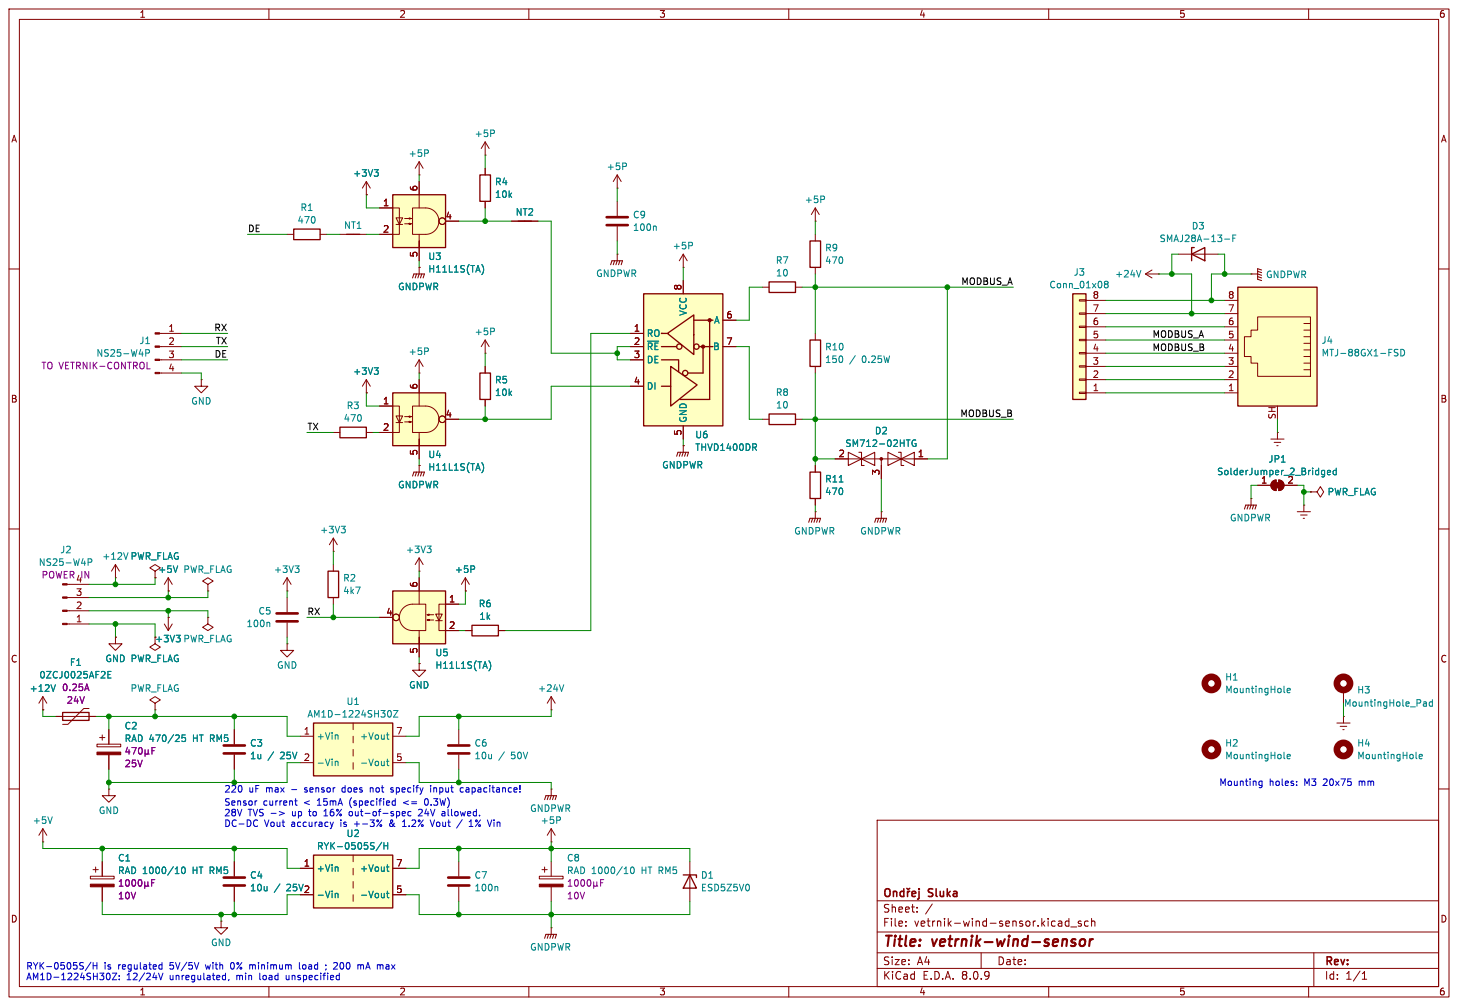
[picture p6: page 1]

Id: 1/1 Title: vetrnik-wind-sensor File: vetrnik-wind-sensor.kicad_sch Sheet: / þÿOndYej Sluka GND

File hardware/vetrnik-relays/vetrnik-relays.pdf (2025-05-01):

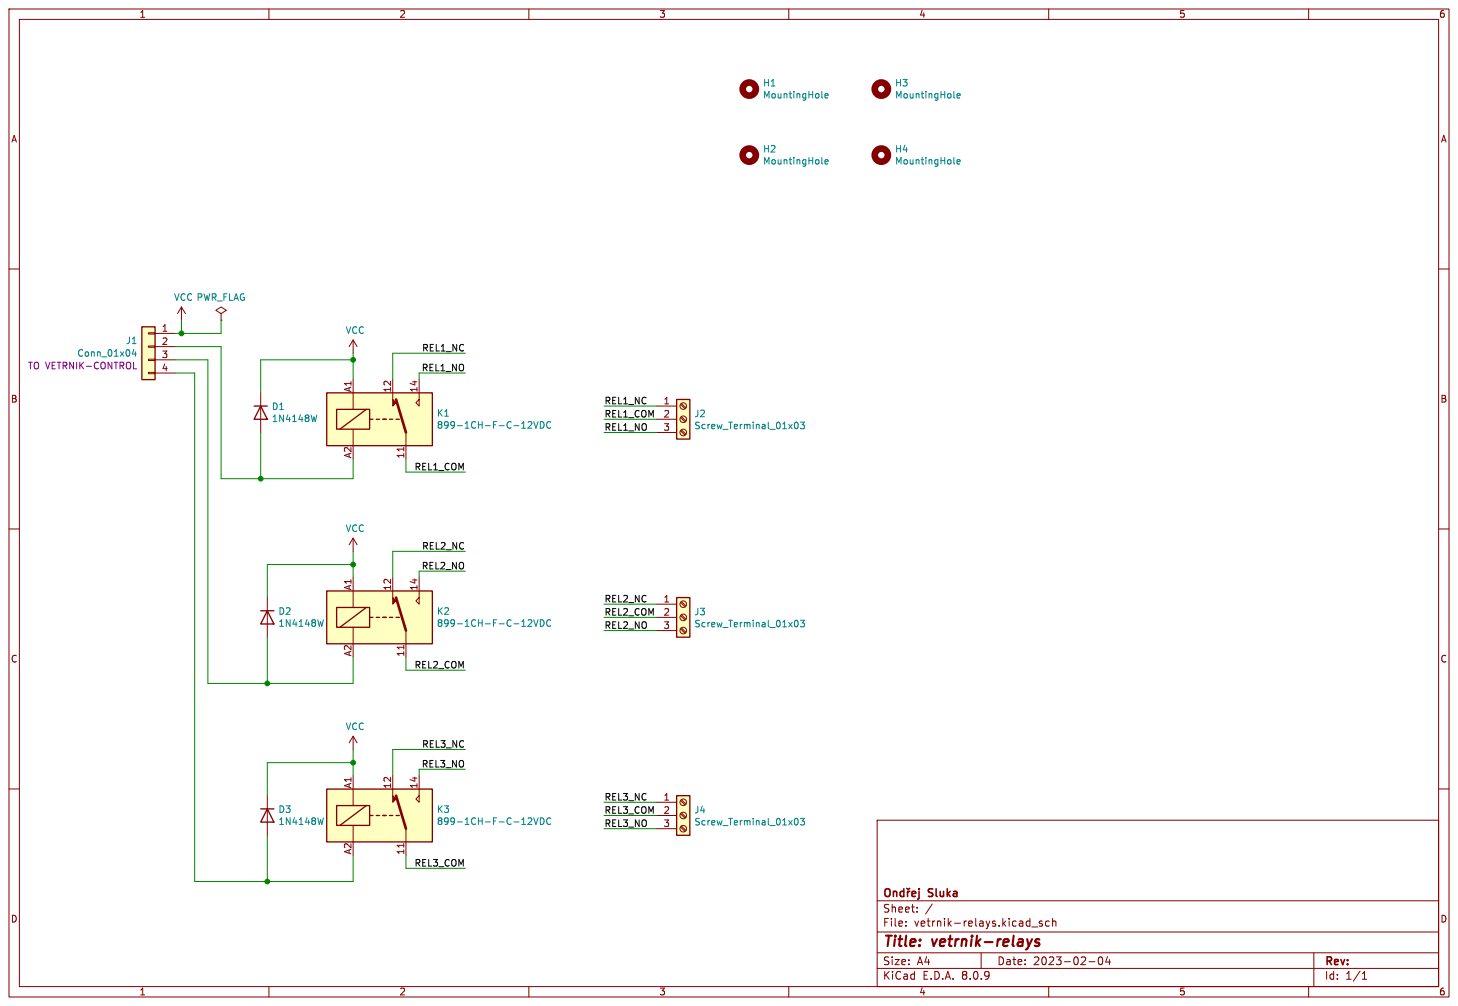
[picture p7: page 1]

File: vetrnik-relays.kicad_sch Sheet: / þÿOndYej Sluka

Id: 1/1 Title: vetrnik-relays

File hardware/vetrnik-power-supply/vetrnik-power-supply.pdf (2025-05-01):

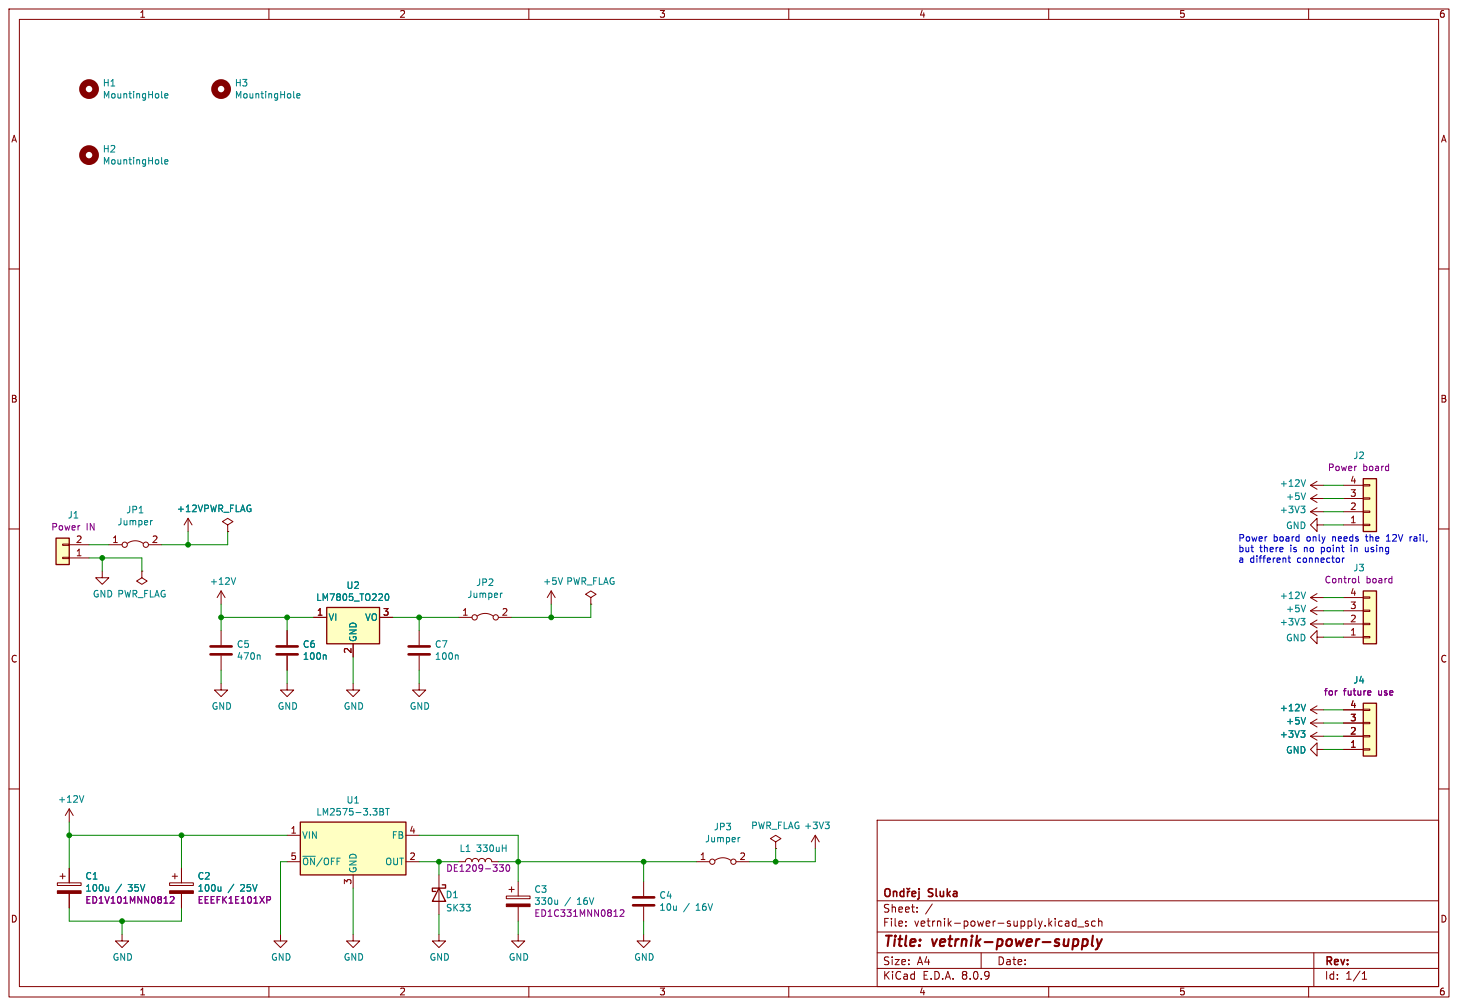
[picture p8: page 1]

Power board only needs the 12V rail, but there is no point in using

File: vetrnik-power-supply.kicad_sch Sheet: / þÿOndYej Sluka GND

Id: 1/1 Title: vetrnik-power-supply

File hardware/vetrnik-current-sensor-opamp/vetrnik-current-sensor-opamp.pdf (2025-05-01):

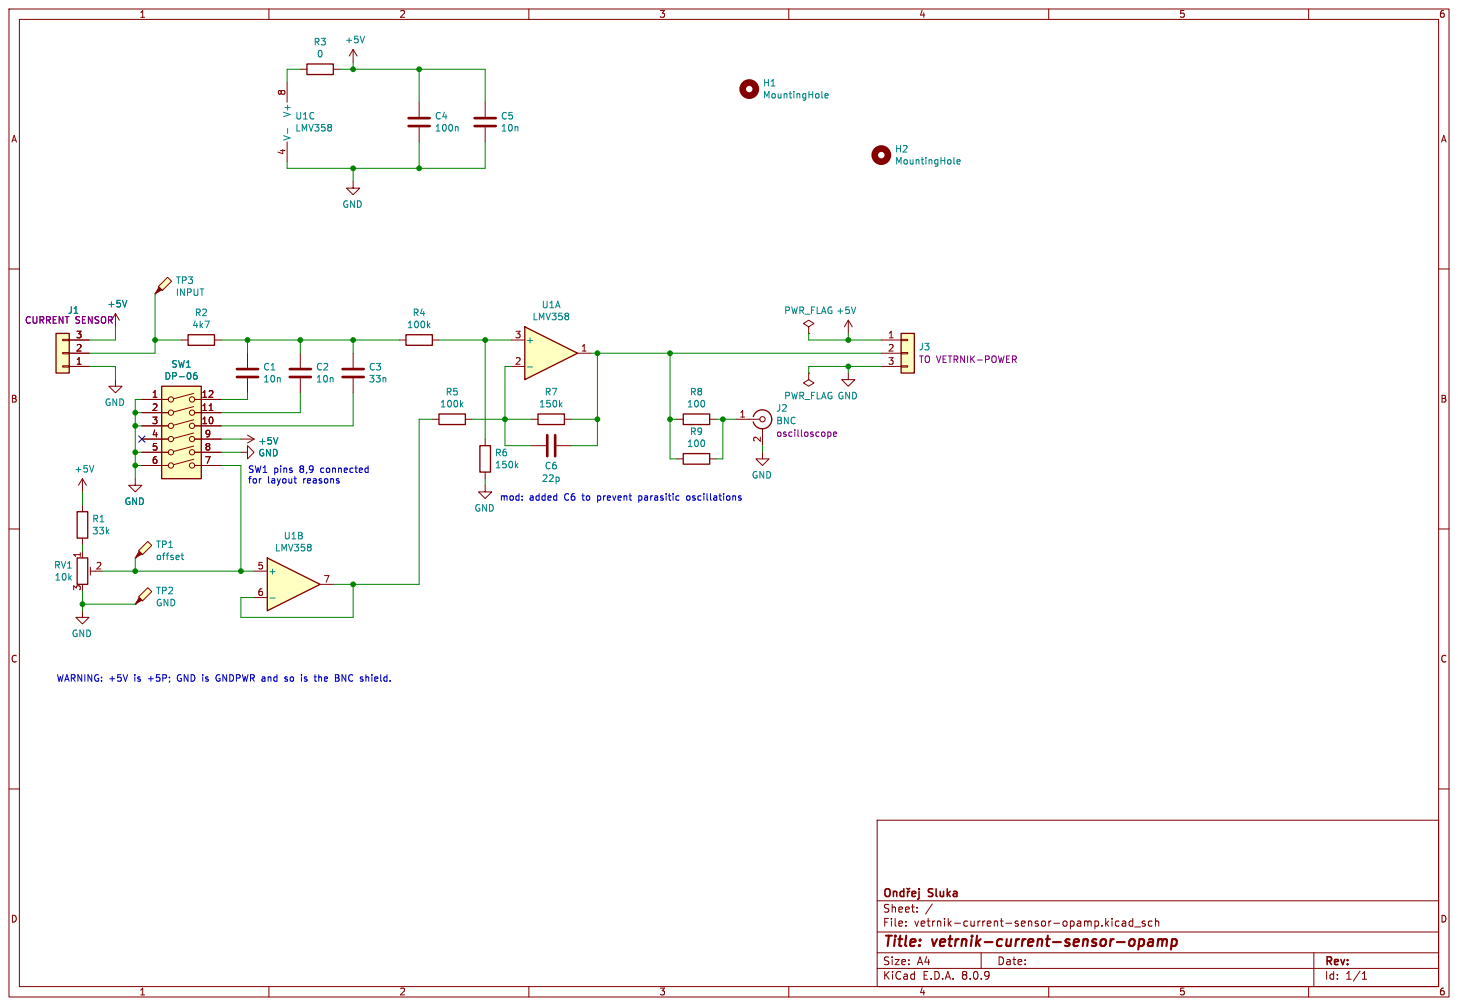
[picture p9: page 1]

File: vetrnik-current-sensor-opamp.kicad_sch Sheet: / þÿOndYej Sluka

Id: 1/1 Title: vetrnik-current-sensor-opamp

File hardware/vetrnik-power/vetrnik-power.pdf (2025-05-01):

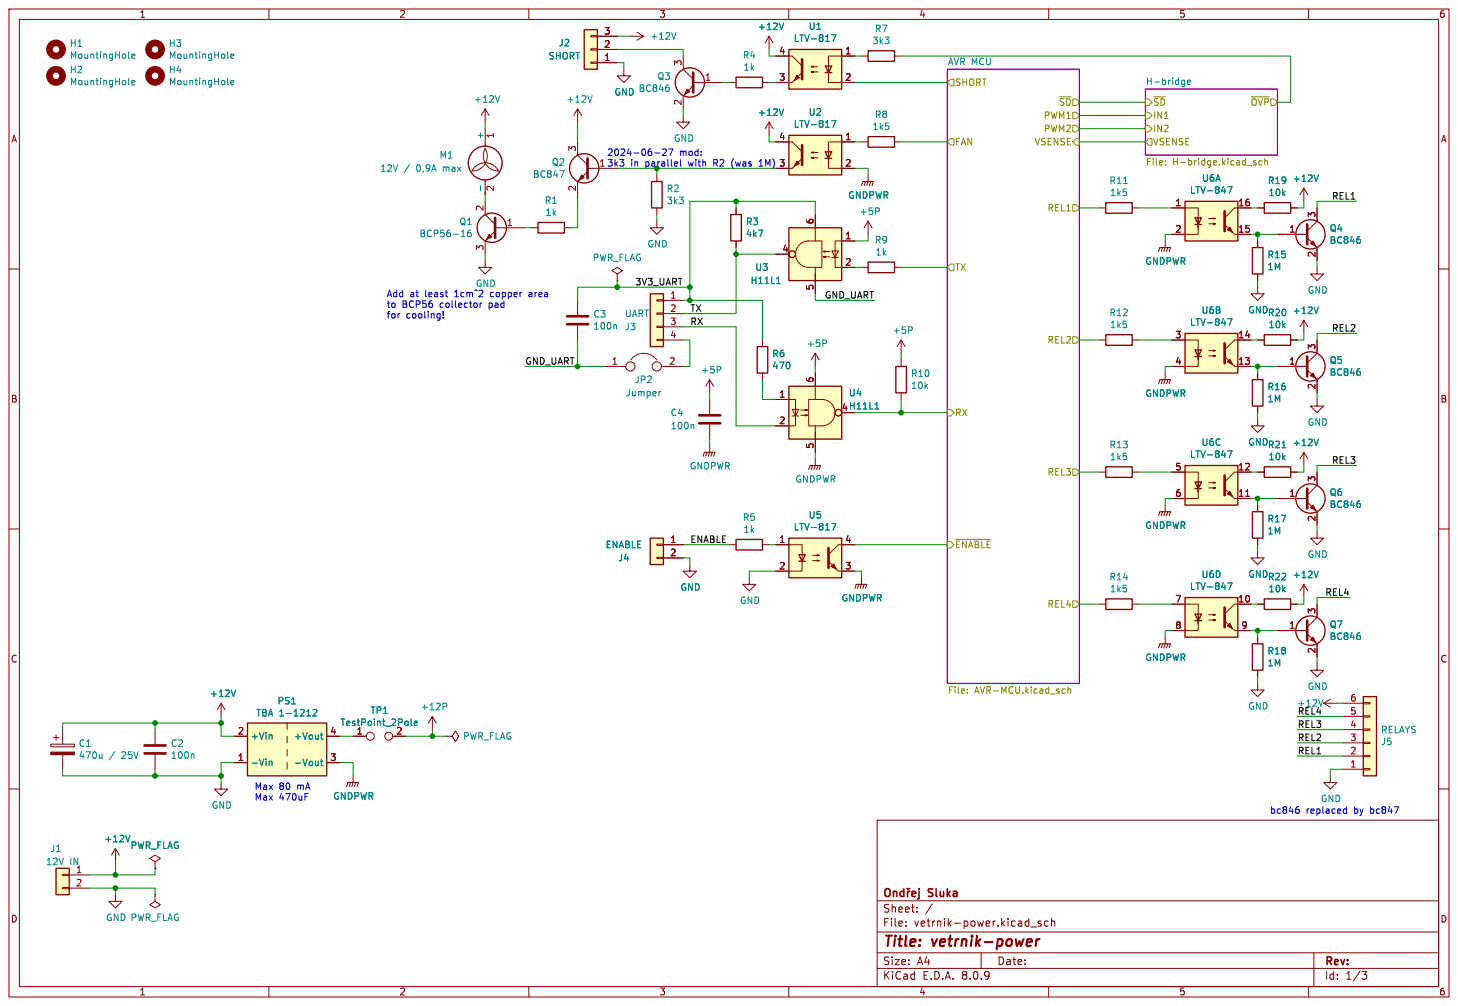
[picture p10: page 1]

Add at least 1cm^2 copper area

Id: 1/3 Title: vetrnik-power File: vetrnik-power.kicad_sch Sheet: / þÿOndYej Sluka

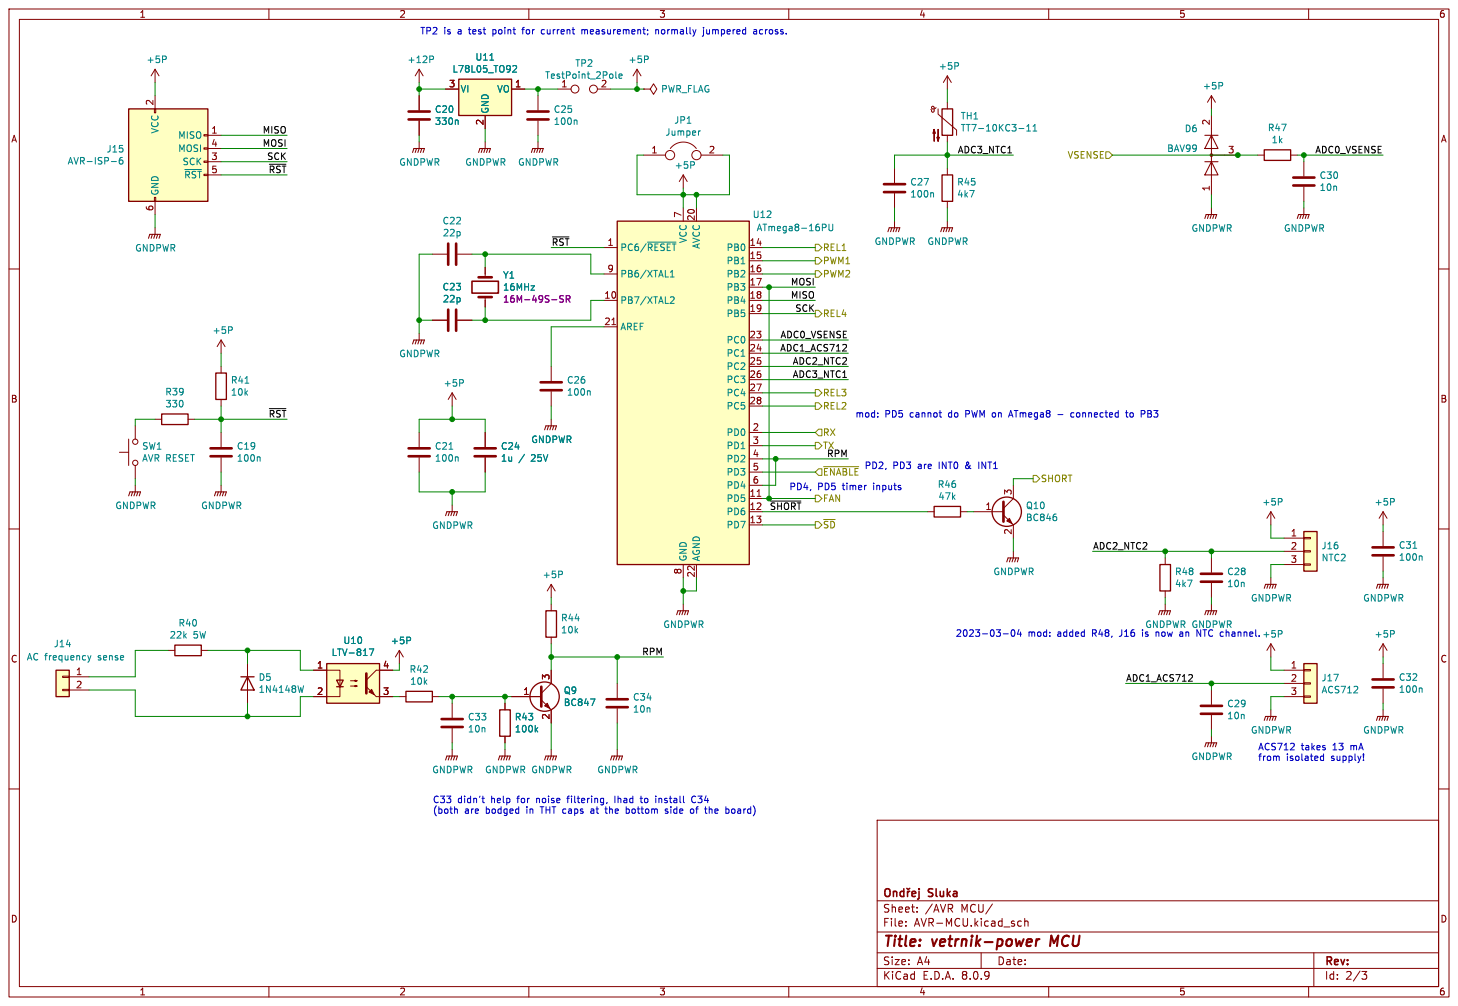
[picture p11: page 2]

2 SCK 3 MOSI 4 ~{RST}5 GND

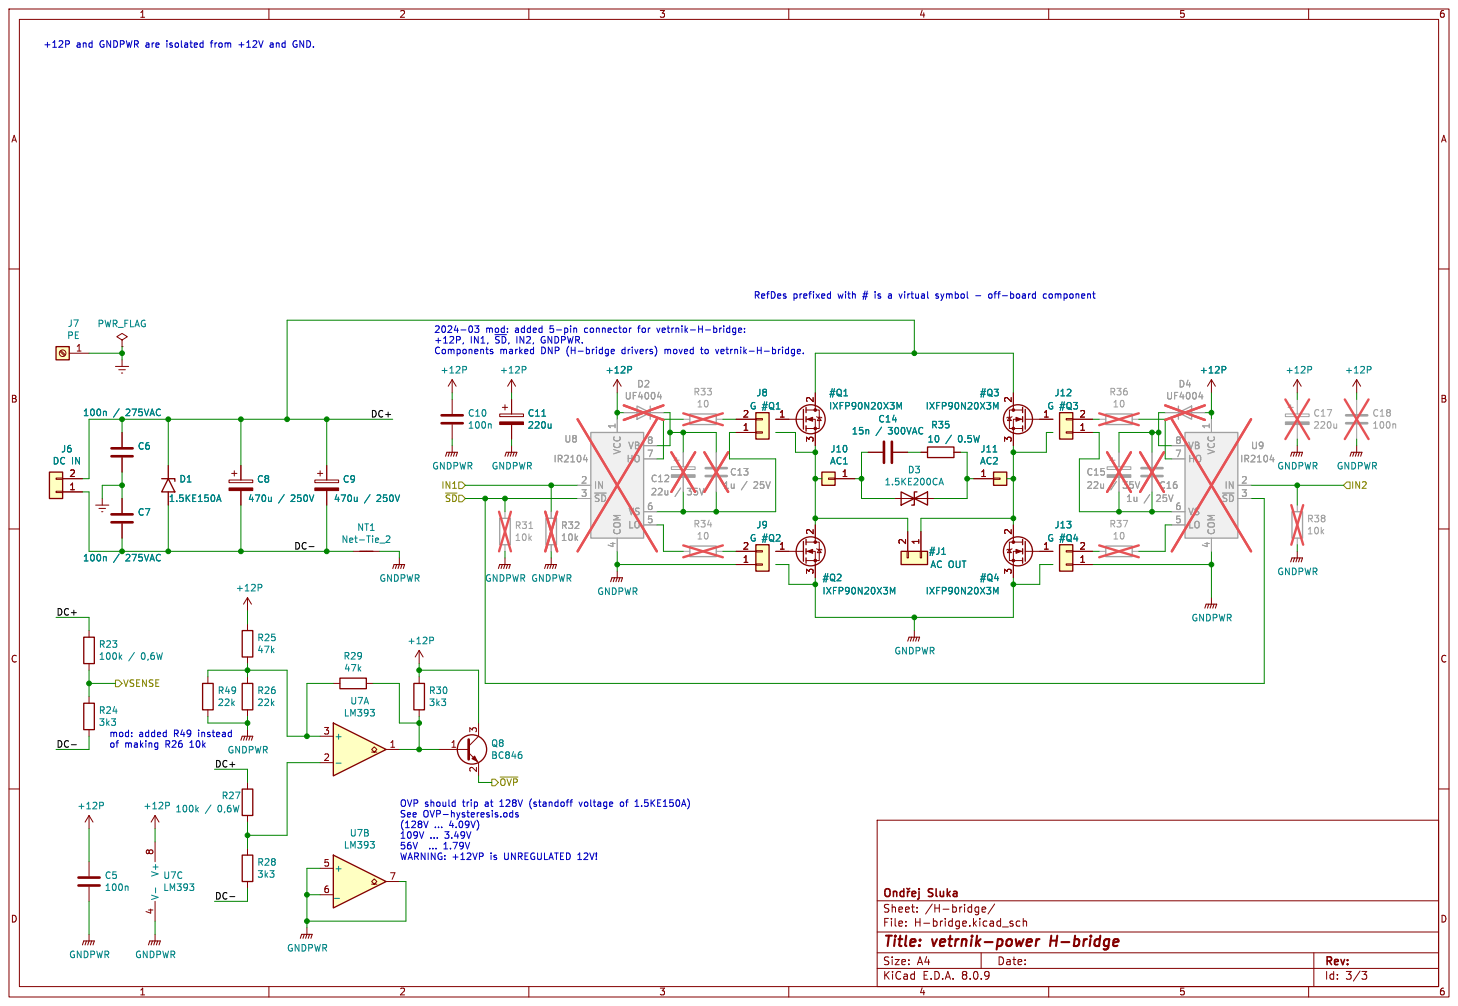
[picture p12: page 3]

þÿOndYej Sluka
File: H-bridge.kicad_sch Sheet: /H-bridge/

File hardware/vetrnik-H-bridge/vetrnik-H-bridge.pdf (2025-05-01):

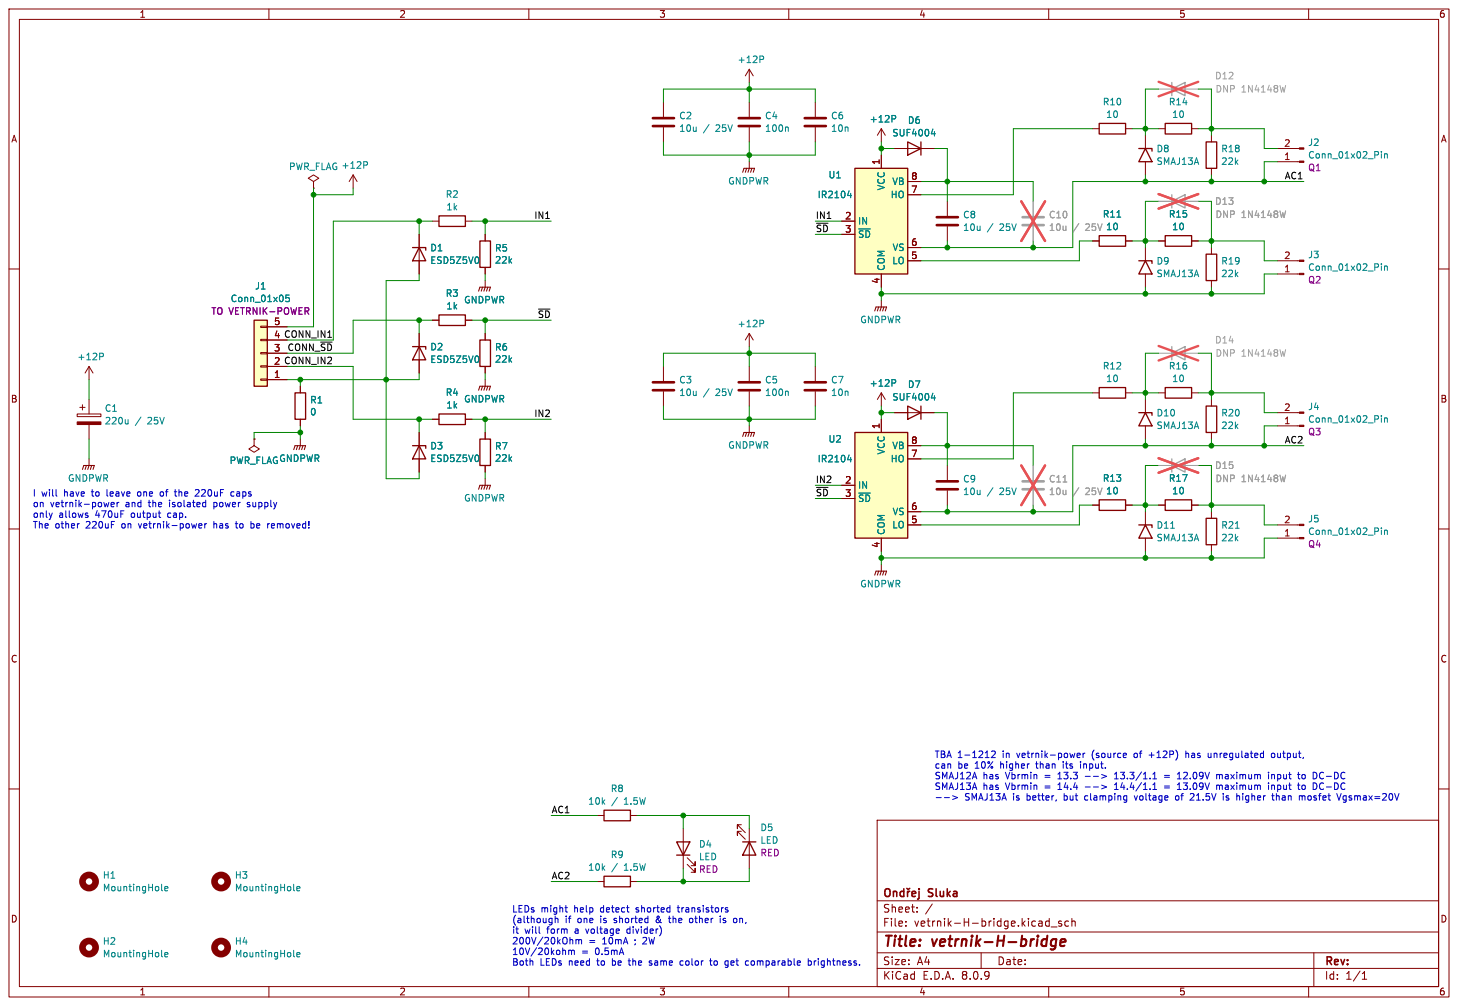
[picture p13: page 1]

File: vetrnik-H-bridge.kicad_sch Sheet: / þÿOndYej Sluka

LEDs might help detect shorted transistors

Id: 1/1 Title: vetrnik-H-bridge

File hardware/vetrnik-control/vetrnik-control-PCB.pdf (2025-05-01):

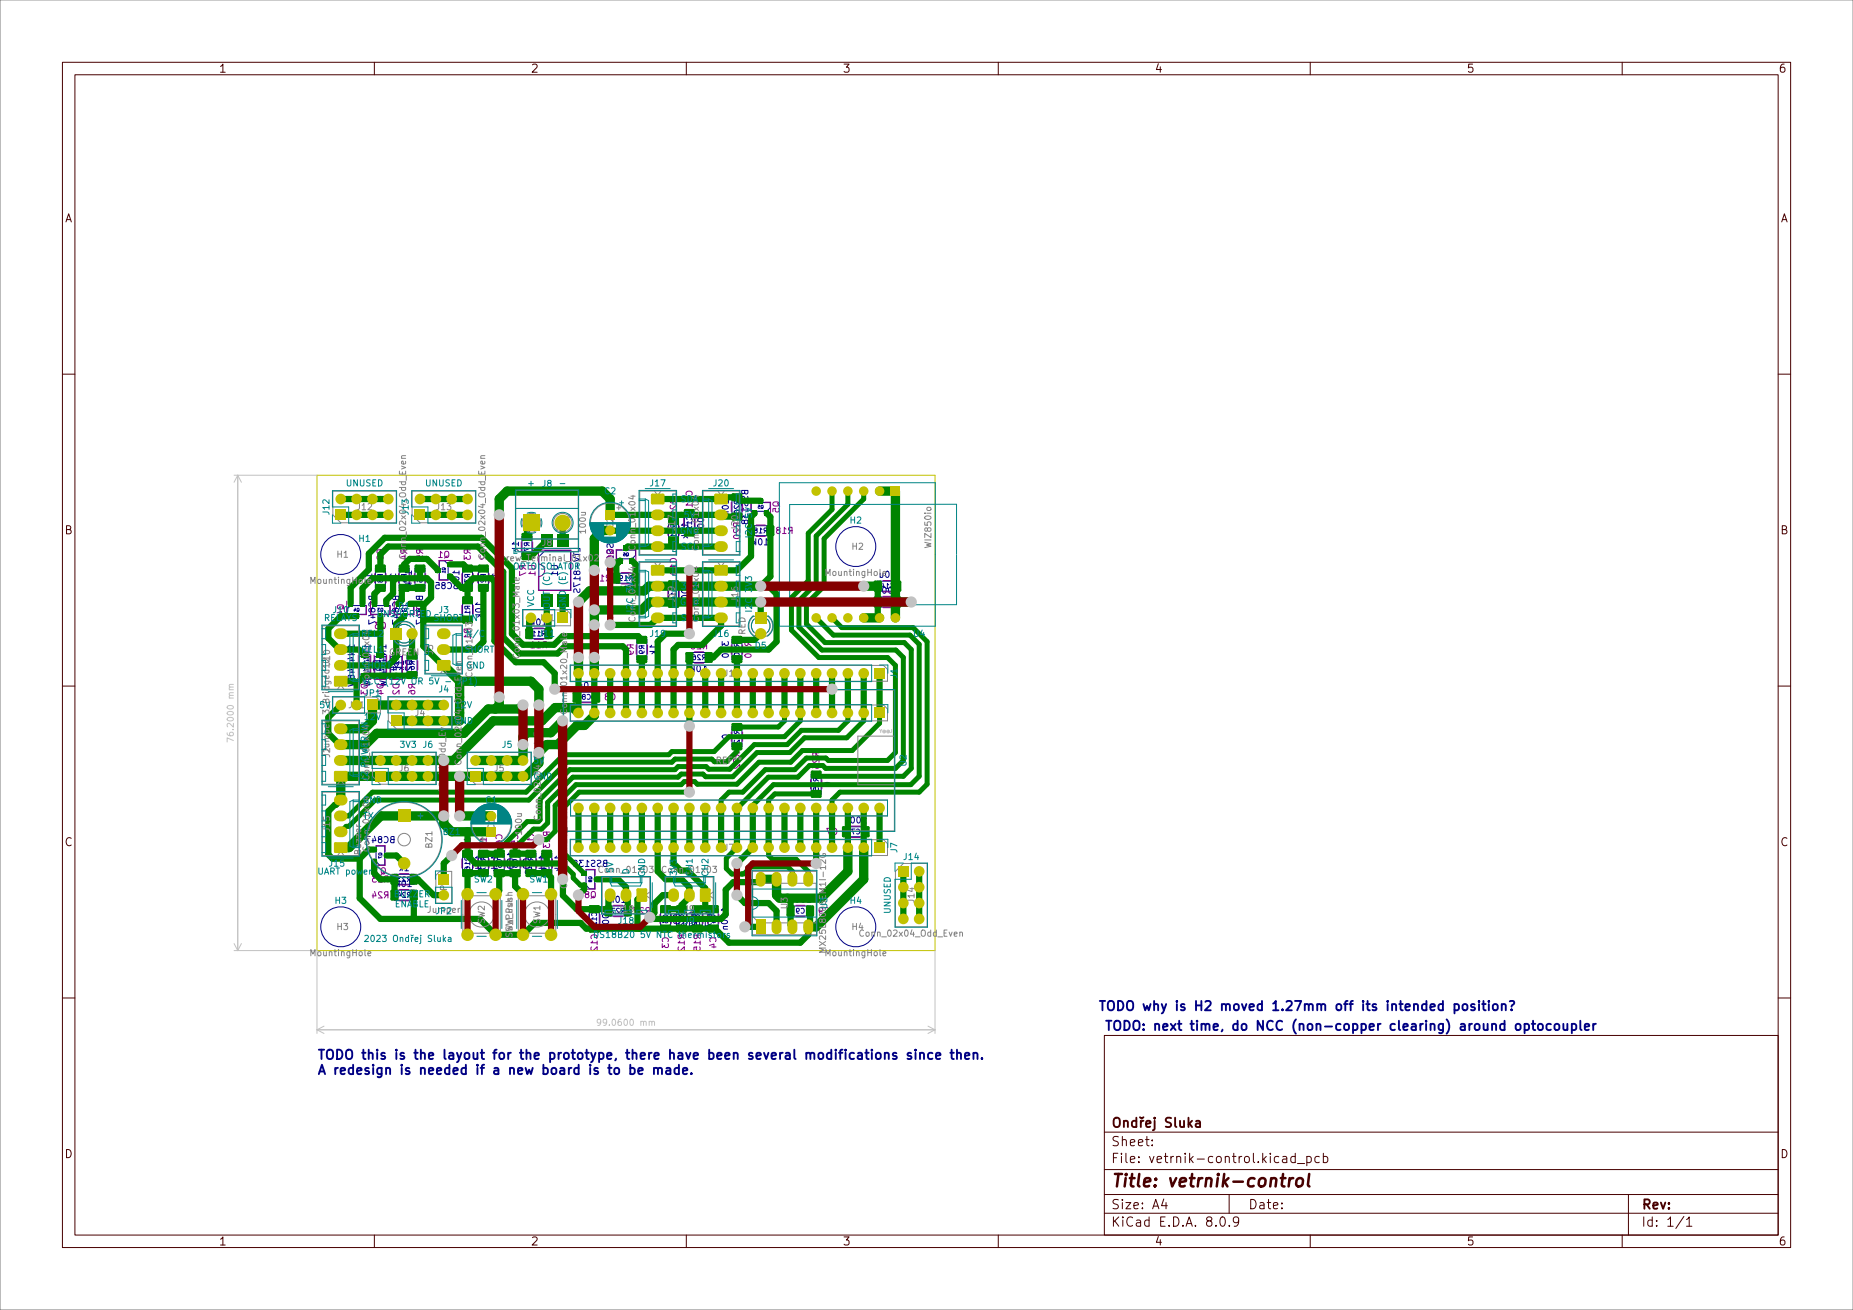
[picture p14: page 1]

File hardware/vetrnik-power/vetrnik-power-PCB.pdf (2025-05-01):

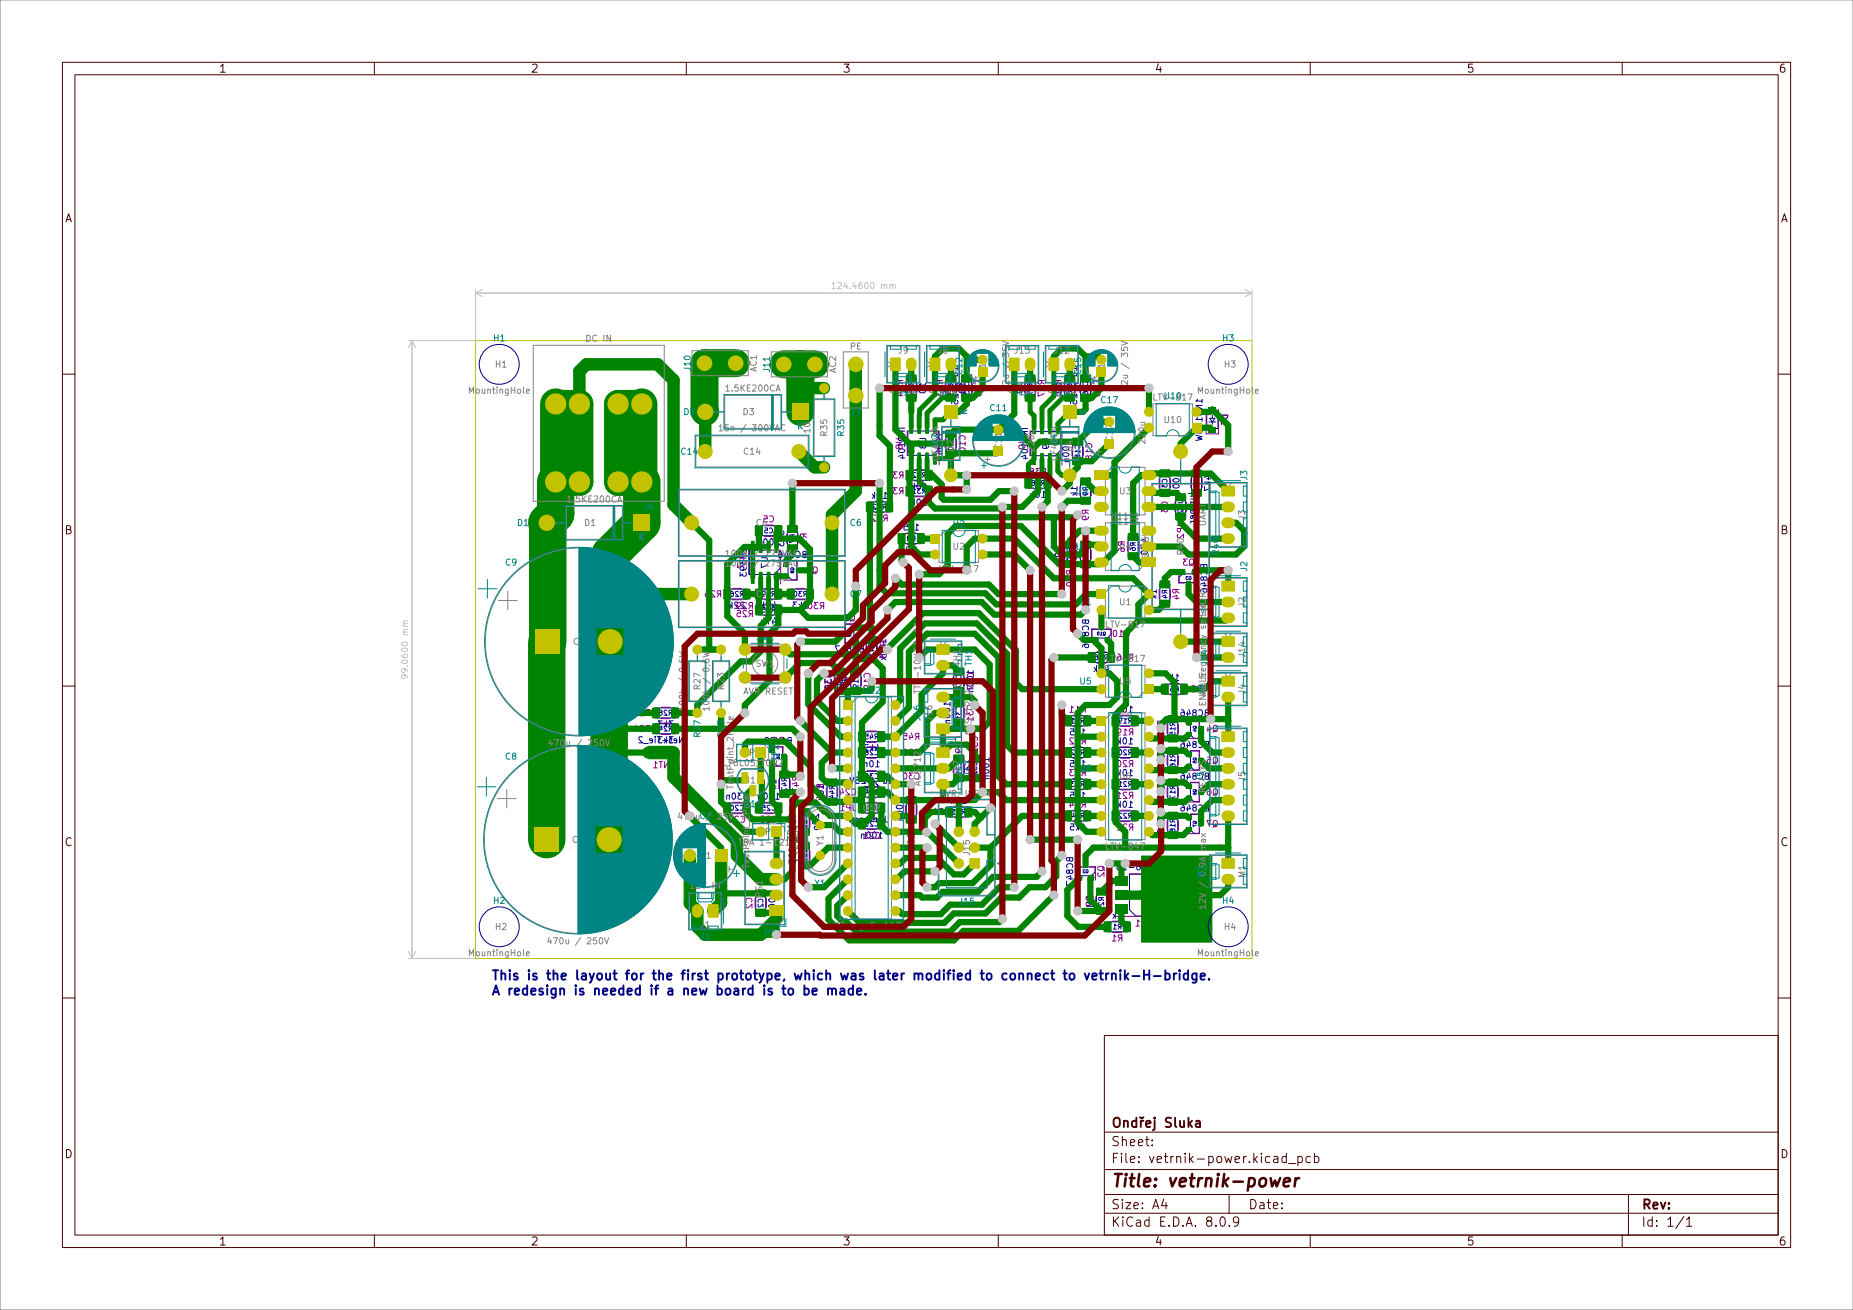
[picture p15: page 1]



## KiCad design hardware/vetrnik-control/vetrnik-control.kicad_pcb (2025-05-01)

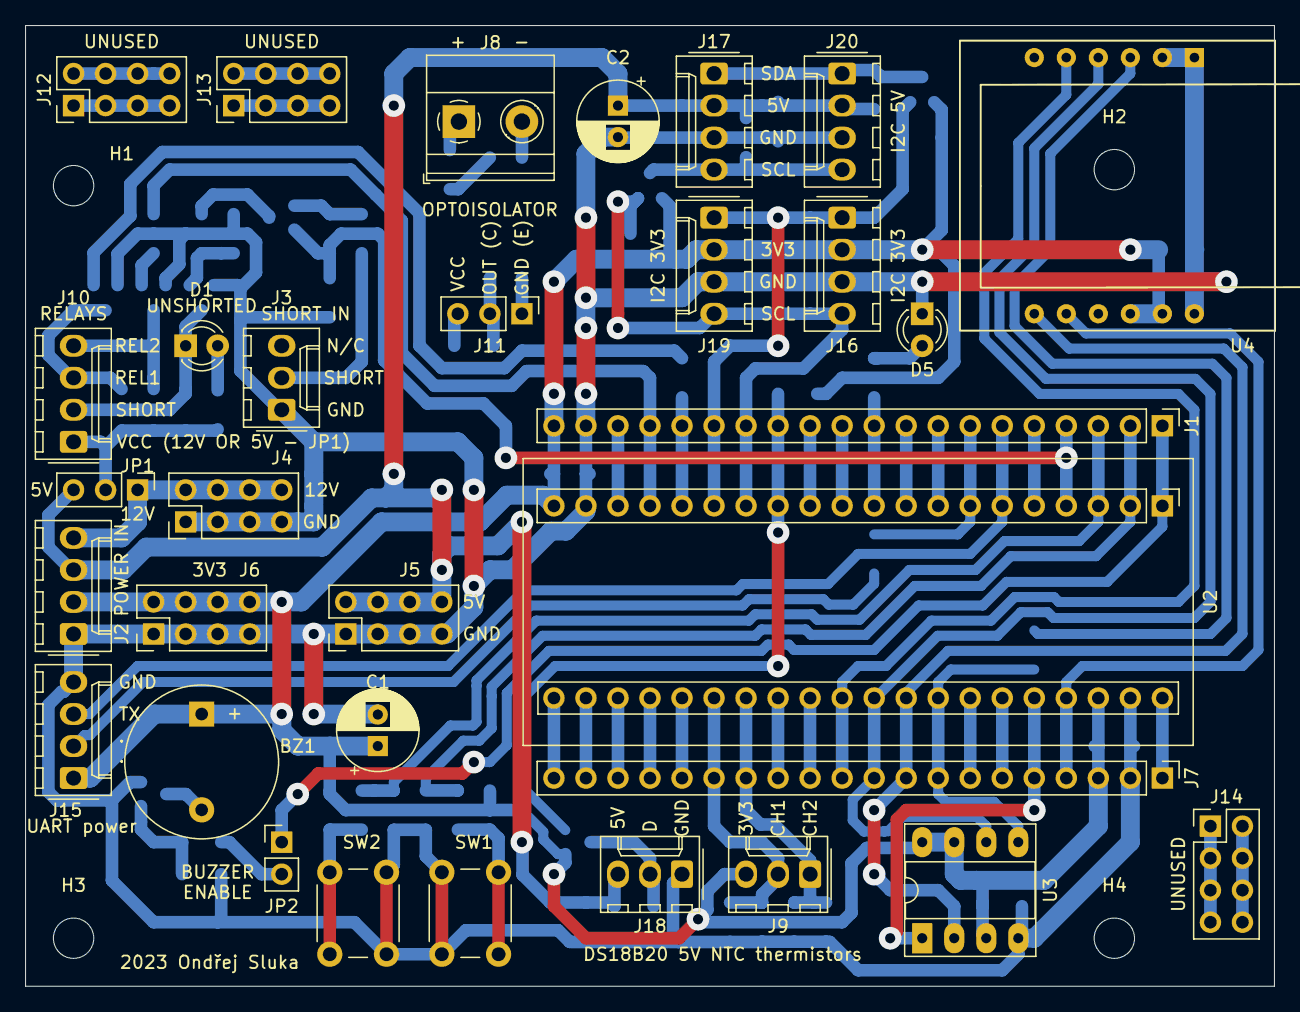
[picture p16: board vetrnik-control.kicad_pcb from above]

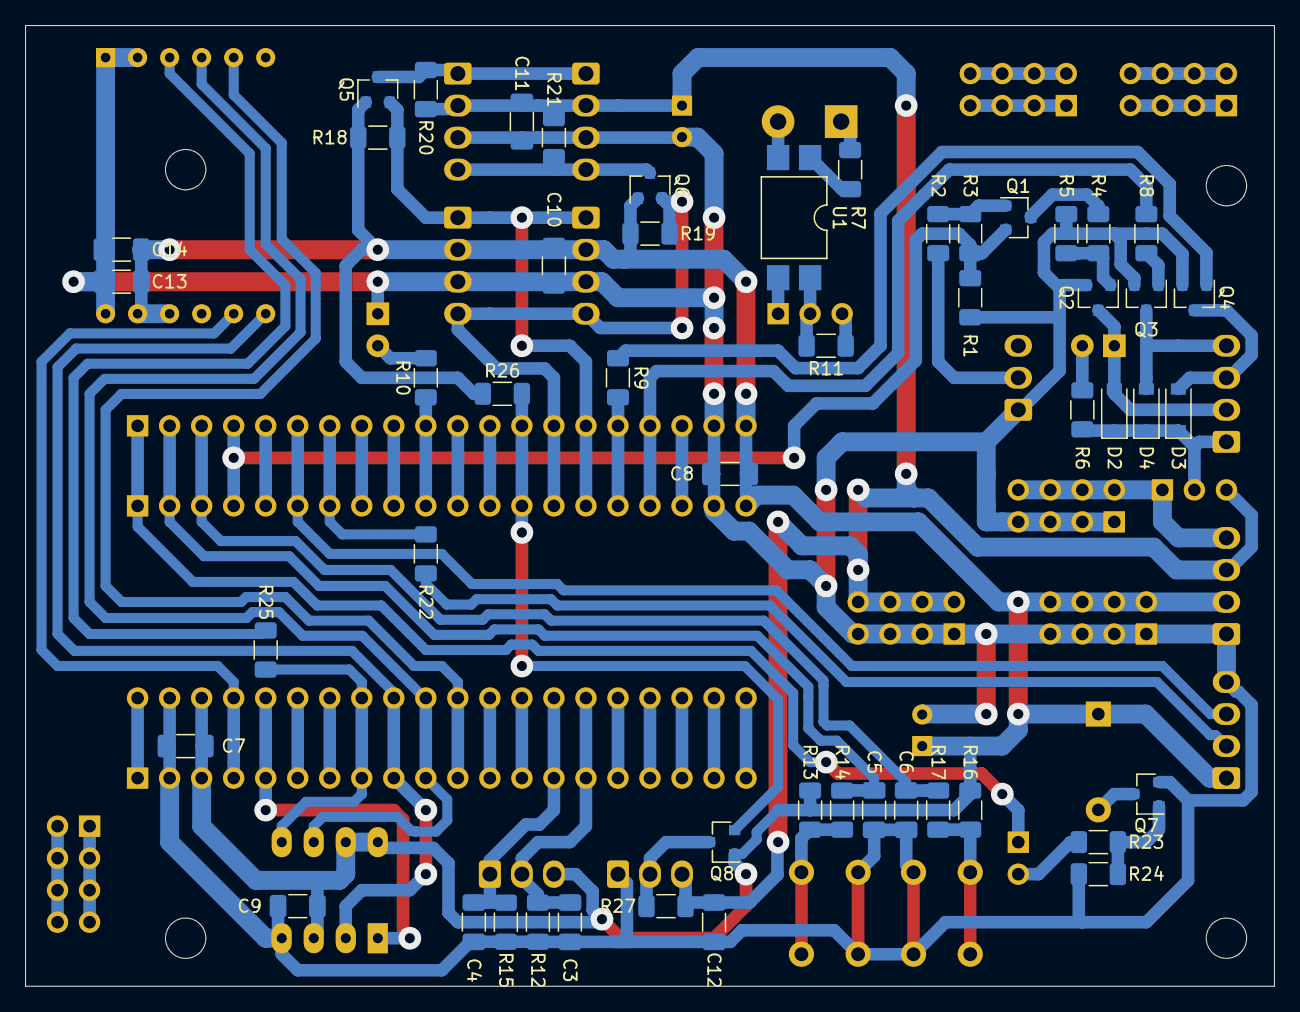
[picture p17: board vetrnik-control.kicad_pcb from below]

Board: 2 copper layers, 99.1 x 76.2 mm, 87 parts (51 on the bottom side), 74 nets.

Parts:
BZ1: Buzzer; Buzzer_12x9.5RM7.6
C1, C2: 100u; CP_Radial_D6.3mm_P2.50mm
C3, C4, C5, C6, C7, C9, C10, C11, C12, C13: 100n; C_1206_3216Metric_Pad1.33x1.80mm_HandSolder
C8, C14: 10u; C_1206_3216Metric_Pad1.33x1.80mm_HandSolder
D1: GREEN; LED_D3.0mm
D2, D3, D4: 1N4148W; D_SOD-123
D5: RED; LED_D3.0mm
H1, H2, H3, H4: MountingHole; MountingHole_3.2mm_M3
J1, J7: Conn_01x20_Male; PinHeader_1x20_P2.54mm_Vertical
J2, J10, J15, J16, J17, J19, J20: Conn_01x04; Molex_KK-254_AE-6410-04A_1x04_P2.54mm_Vertical
J3, J9, J18: Conn_01x03; Molex_KK-254_AE-6410-03A_1x03_P2.54mm_Vertical
J4, J5, J6, J12, J13, J14: Conn_02x04_Odd_Even; PinHeader_2x04_P2.54mm_Vertical
J8: Screw_Terminal_01x02; TerminalBlock_Phoenix_MKDS-1,5-2_1x02_P5.00mm_Horizontal
J11: Conn_01x03_Male; PinHeader_1x03_P2.54mm_Vertical
JP1: Jumper_3_Bridged12; PinHeader_1x03_P2.54mm_Vertical
JP2: Jumper; PinHeader_1x02_P2.54mm_Vertical
Q1: BC857; SOT-23
Q2, Q3, Q4, Q7: BC847; SOT-23
Q5, Q6, Q8: BSS138; SOT-23
R1, R3, R5, R11, R13, R14, R16, R17, R18, R19, R20, R21, R24, R26, R27: 10k; R_1206_3216Metric_Pad1.30x1.75mm_HandSolder
R2, R4, R6, R7, R8, R9, R23: 1k; R_1206_3216Metric_Pad1.30x1.75mm_HandSolder
R10: 330; R_1206_3216Metric_Pad1.30x1.75mm_HandSolder
R12, R15: 4k7; R_1206_3216Metric_Pad1.30x1.75mm_HandSolder
R22, R25: 0; R_1206_3216Metric_Pad1.30x1.75mm_HandSolder
SW1, SW2: SW_Push; SW_PUSH_6mm_H4.3mm
U1: LTV-817S; SMDIP-4_W9.53mm
U2: YAAJ_WeAct_BlackPill_Part_Like; YAAJ_WeAct_BlackPill_2
U3: MX25L8006EM1I-12G; DIP-8_W7.62mm_Socket_LongPads
U4: WIZ850io

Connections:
+3V3: BZ1.1, C1.1, C7.1, C8.1, C9.1, C10.1, C13.1, C14.1, J1.20, J2.2, J6.2, J6.4, J6.6, J6.8, J7.3, J9.3, J15.1, J16.2, J19.2, Q5.1, Q6.1, Q8.1, R13.1, R16.1, R18.1, R19.1, R26.1, U2.20, U2.38, U3.3, U3.7, U3.8, U4.10, U4.11
+5V: C2.1, C11.1, C12.1, J2.3, J5.2, J5.4, J5.6, J5.8, J17.2, J18.3, J20.2, JP1.3, R20.1, R21.1, R27.1
+12V: J2.4, J4.2, J4.4, J4.6, J4.8, JP1.1
/ADC_NTC1: C3.1, J7.15, J9.2, R12.1, U2.26
/ADC_NTC2: C4.1, J7.14, J9.1, R15.1, U2.27
/BUTTON1: C5.1, J1.2, R14.1, U2.2
/BUTTON2: C6.1, J1.3, R17.1, U2.3
/BUZZER: J1.1, JP2.1, U2.1
/MCU_18: J1.18, U2.18
/MCU_40: J7.1, U2.40
/MISO: J7.9, U2.32, U3.2, U4.7
/MOSI: J7.8, R25.2, U2.33, U3.5
/PA2: J7.13, U2.28
/PA3: J7.12, U2.29
/PA4: J7.11, U2.30, U4.5
/PA5: J7.10, U2.31, U3.6, U4.4
/PA8: J1.5, U2.5
/PA9: J1.6, J15.3, U2.6
/PA10: J1.7, R22.2, U2.7
/PA11: J1.8, U2.8
/PA12: J1.9, U2.9
/PA15: J1.10, R10.1, U2.10
/PB0: J7.7, U2.34
/PB1: J7.6, U2.35
/PB2: J7.5, U2.36, U3.1
/PB3: J1.11, U2.11
/PB4: J1.12, U2.12
/PB5: J1.13, Q8.2, R26.2, U2.13
/PB6: J1.14, J16.4, J19.4, Q6.2, R19.2, U2.14
/PB7: J1.15, J16.1, J19.1, Q5.2, R18.2, U2.15
/PB8: J1.16, R9.2, U2.16
/PB9: J1.17, R8.2, U2.17
/PB10: J7.4, U2.37, U4.8
/PB15: J1.4, Q1.2, R1.1, R3.1, U2.4
/PC13: J7.19, U2.22
/PC14: J7.18, U2.23
/PC15: J7.17, U2.24
/RES: J7.16, U2.25
/SCL_5V: J17.4, J20.4, Q6.3, R21.2
/SDA_5V: J17.1, J20.1, Q5.3, R20.2
/VBat: J7.20, U2.21
/onewire_5V: J18.2, Q8.3, R27.2
GND: C1.2, C2.2, C3.2, C4.2, C5.2, C6.2, C7.2, C8.2, C9.2, C10.2, C11.2, C12.2, C13.2, C14.2, D5.1, J1.19, J2.1, J3.1, J4.1, J4.3, J4.5, J4.7, J5.1, J5.3, J5.5, J5.7, J6.1, J6.3, J6.5, J6.7, J7.2, J15.4, J16.3, J17.3, J18.1, J19.3, J20.3, Q2.2, Q3.2, Q4.2, Q7.2, R1.2, R5.2, R12.2, R15.2, R24.2, SW1.2, SW2.2, U2.19, U2.39, U3.4, U4.1, U4.2, U4.12
unnamed: BZ1.2, Q7.3
unnamed: D1.1, D2.2, J10.2, Q2.3
unnamed: D1.2, R6.2
unnamed: D2.1, D3.1, D4.1, J10.1, JP1.2, R6.1
unnamed: D3.2, J10.3, Q4.3
unnamed: D4.2, J10.4, Q3.3
unnamed: D5.2, R10.2
unnamed: J3.2, R2.2
unnamed: J8.1, R7.2
unnamed: J8.2, U1.2
unnamed: J11.1, U1.3
unnamed: J11.2, R11.2, U1.4
unnamed: J11.3, R11.1
unnamed: J12.1, J12.3, J12.5, J12.7
unnamed: J12.2, J12.4, J12.6, J12.8
unnamed: J13.1, J13.3, J13.5, J13.7
unnamed: J13.2, J13.4, J13.6, J13.8
unnamed: J14.1, J14.3, J14.5, J14.7
unnamed: J14.2, J14.4, J14.6, J14.8
unnamed: J15.2, R22.1
unnamed: JP2.2, R23.2
unnamed: Q1.1, R2.1, R3.2
unnamed: Q1.3, R4.2
unnamed: Q2.1, R4.1, R5.1
unnamed: Q3.1, R8.1
unnamed: Q4.1, R9.1
unnamed: Q7.1, R23.1, R24.1
unnamed: R7.1, U1.1
unnamed: R13.2, R14.2, SW1.1
unnamed: R16.2, R17.2, SW2.1
unnamed: R25.1, U4.3

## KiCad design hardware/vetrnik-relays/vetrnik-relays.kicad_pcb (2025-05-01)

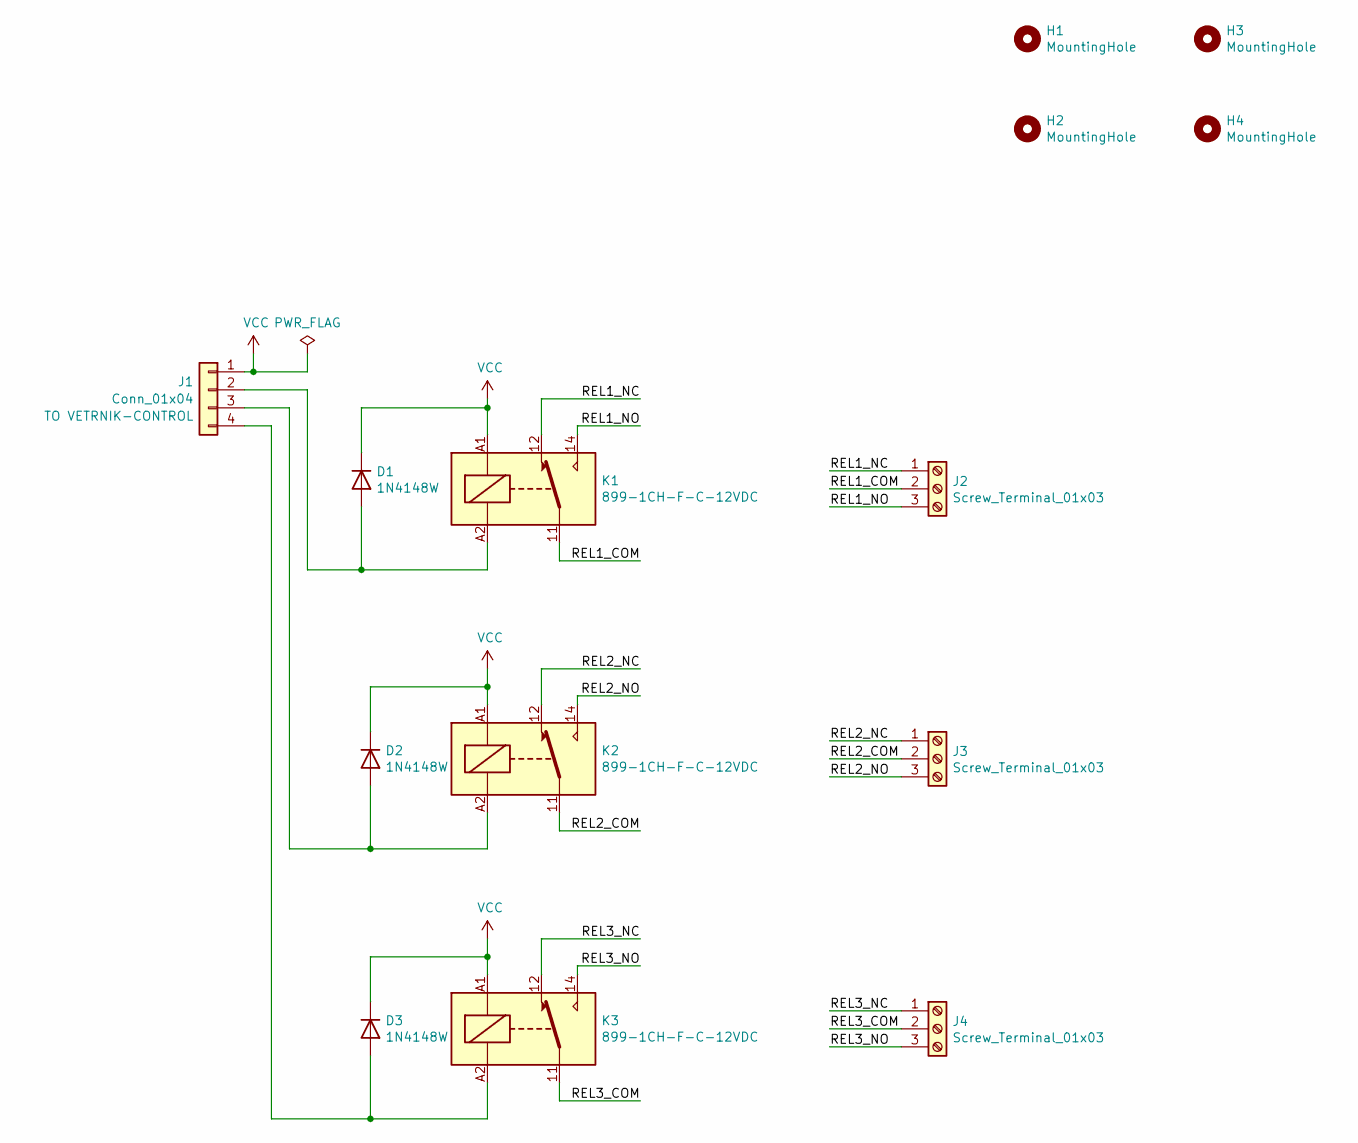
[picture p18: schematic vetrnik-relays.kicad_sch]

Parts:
D1, D2, D3: 1N4148W; D_SOD-123
H1, H2, H3, H4: MountingHole; MountingHole_3.2mm_M3
J1: Conn_01x04; Molex_KK-254_AE-6410-04A_1x04_P2.54mm_Vertical
J2, J3, J4: Screw_Terminal_01x03; TerminalBlock_Phoenix_MKDS-1,5-3_1x03_P5.00mm_Horizontal
K1, K2, K3: 899-1CH-F-C-12VDC; Relay_SPDT_Finder_36.11

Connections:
/REL1_COM: J2.2, K1.11
/REL1_NC: J2.1, K1.12
/REL1_NO: J2.3, K1.14
/REL2_COM: J3.2, K2.11
/REL2_NC: J3.1, K2.12
/REL2_NO: J3.3, K2.14
/REL3_COM: J4.2, K3.11
/REL3_NC: J4.1, K3.12
/REL3_NO: J4.3, K3.14
unnamed: D1.2 (A), J1.2, K1.A2
unnamed: D2.2 (A), J1.3, K2.A2
unnamed: D3.2 (A), J1.4, K3.A2
VCC: D1.1 (K), D2.1 (K), D3.1 (K), J1.1, K1.A1, K2.A1, K3.A1

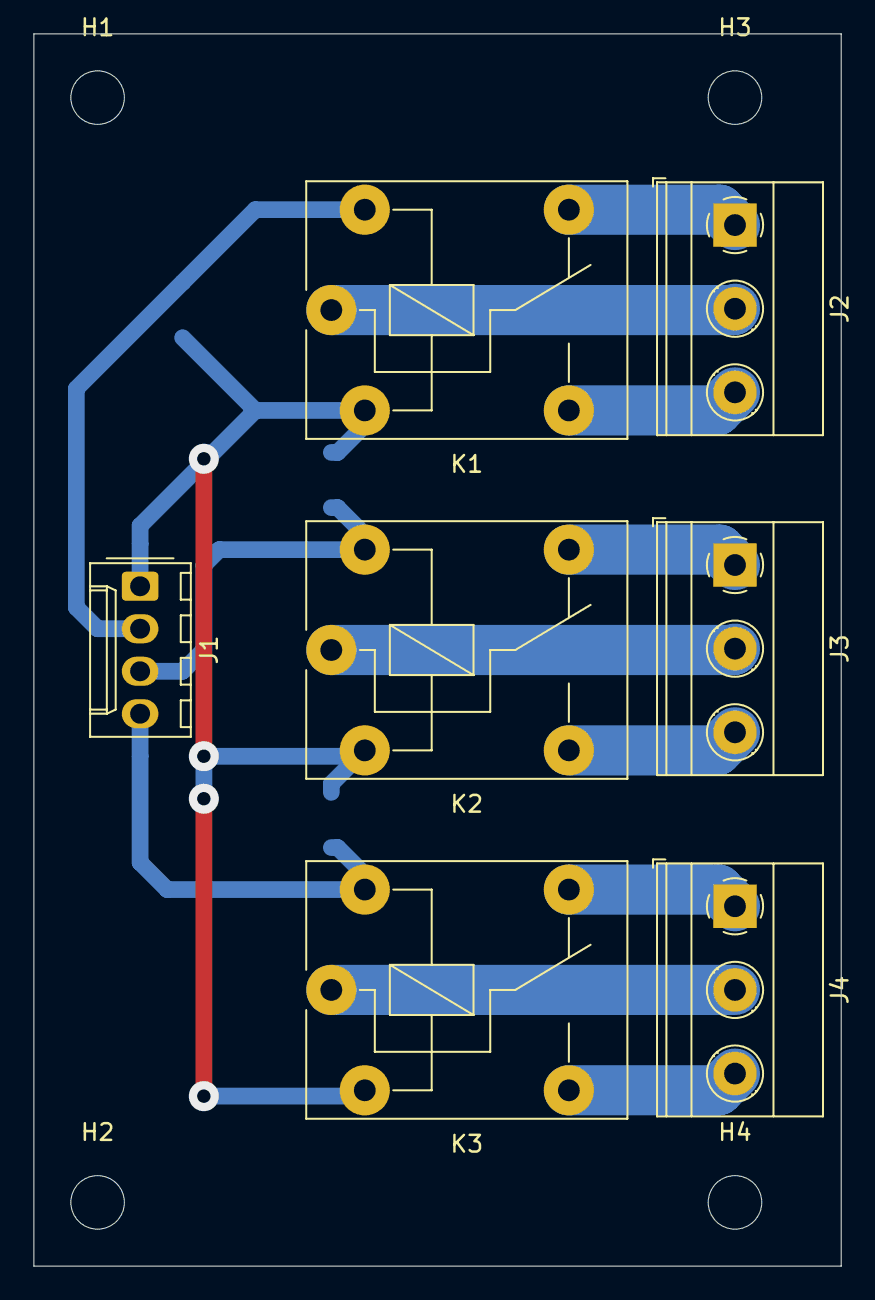
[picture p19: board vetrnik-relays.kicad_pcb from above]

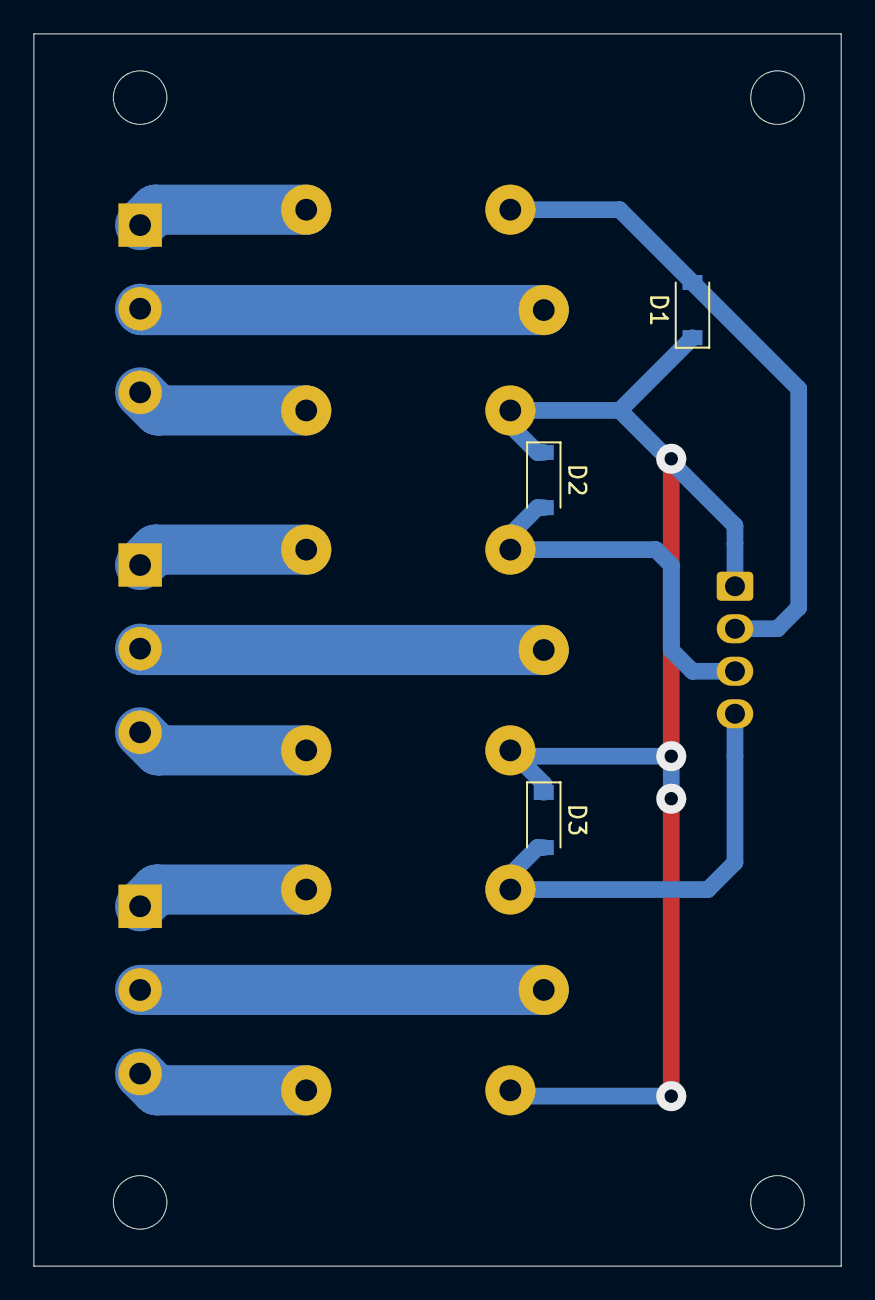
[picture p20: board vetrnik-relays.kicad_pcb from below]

Board: 2 copper layers, 48.3 x 73.7 mm, 14 parts (3 on the bottom side), 13 nets.

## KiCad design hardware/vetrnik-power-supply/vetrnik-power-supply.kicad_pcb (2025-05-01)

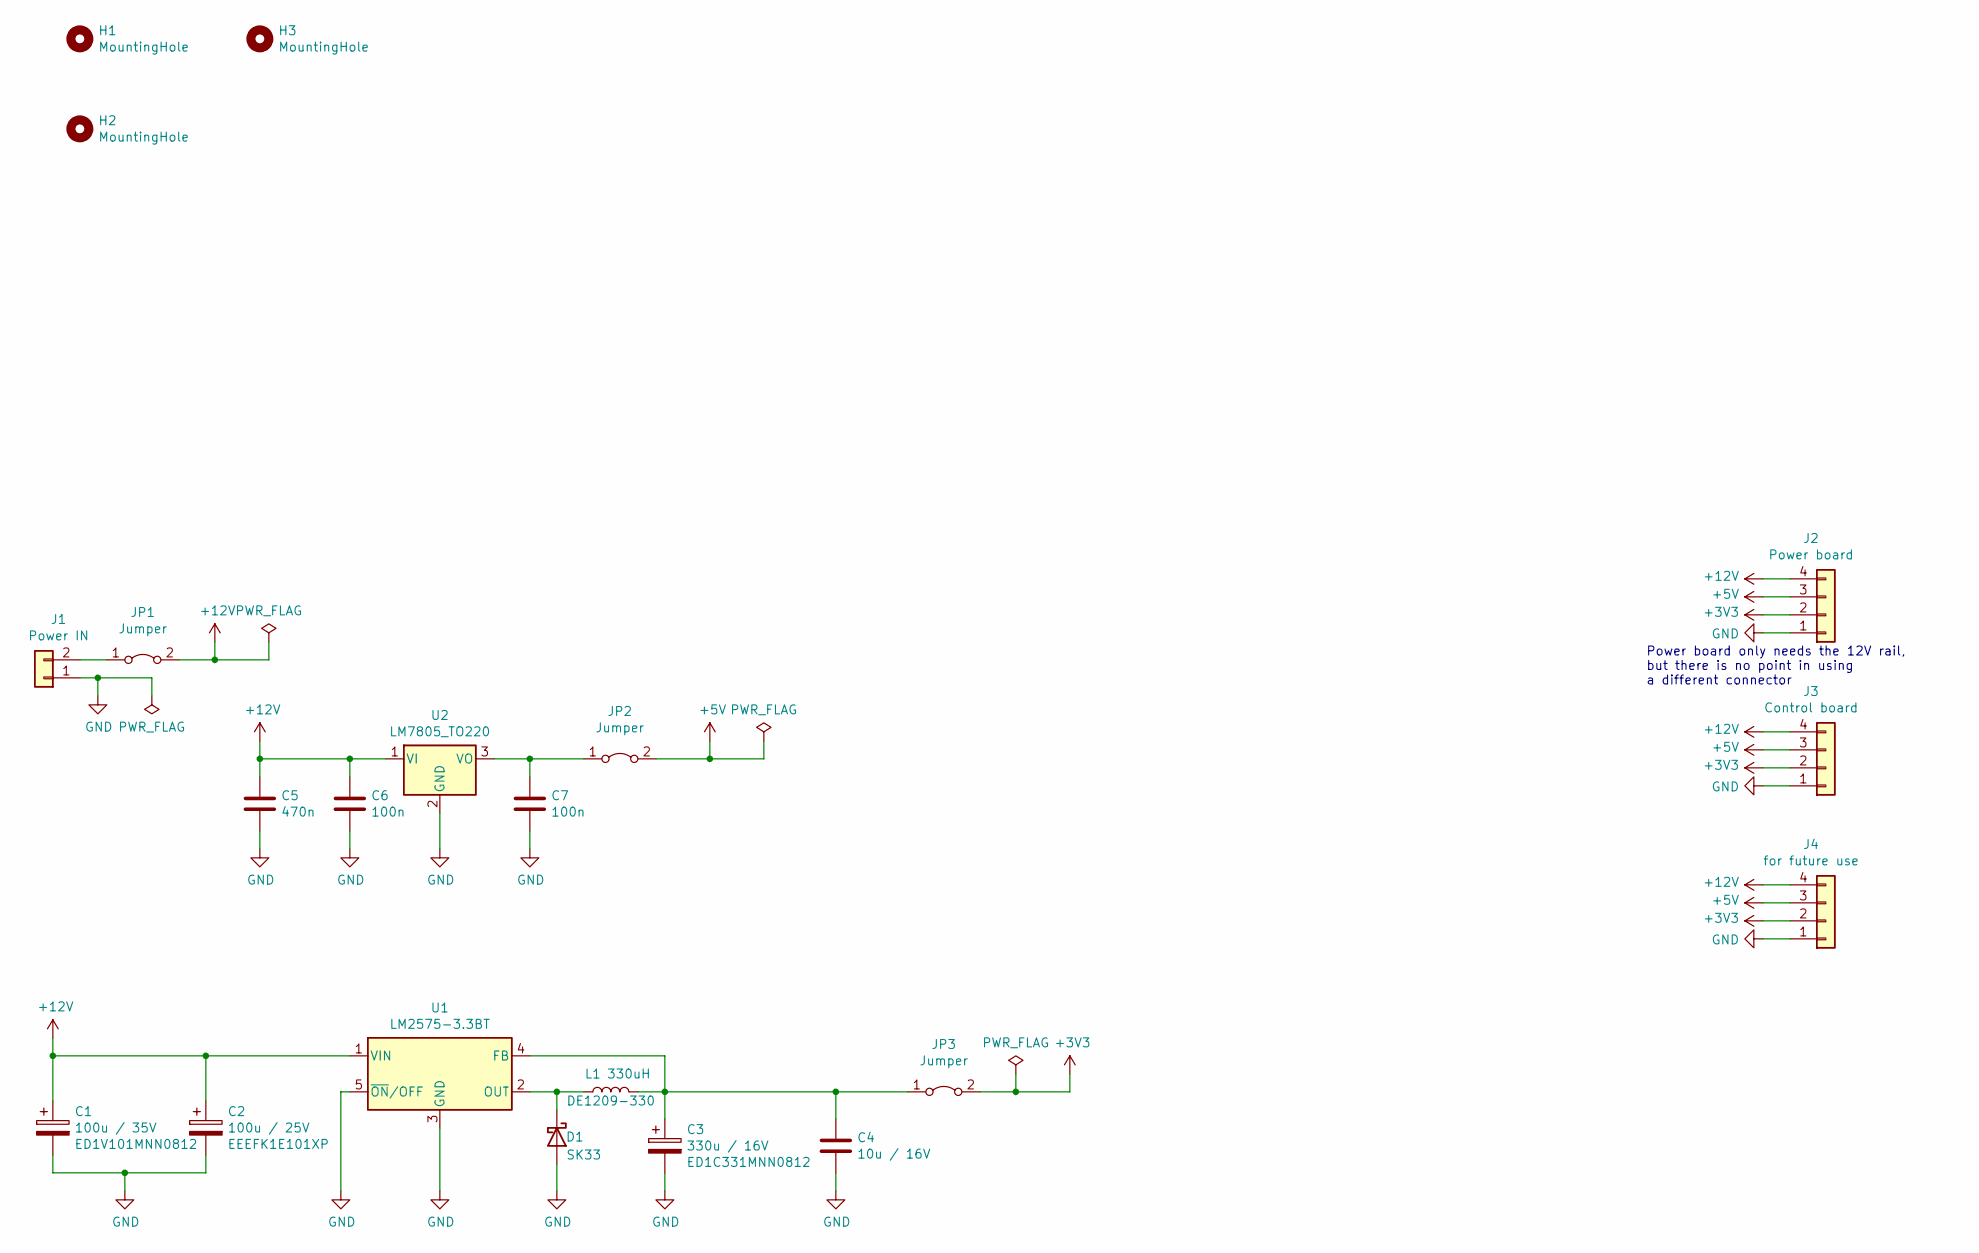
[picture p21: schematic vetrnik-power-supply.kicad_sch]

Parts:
C1: 100u / 35V; CP_Radial_D8.0mm_P3.50mm; Part Number ED1V101MNN0812
C2: 100u / 25V; CP_Elec_6.3x7.7; Part Number EEEFK1E101XP
C3: 330u / 16V; CP_Radial_D8.0mm_P3.50mm; Part Number ED1C331MNN0812
C4: 10u / 16V; C_1206_3216Metric_Pad1.33x1.80mm_HandSolder
C5: 470n; C_1206_3216Metric_Pad1.33x1.80mm_HandSolder
C6, C7: 100n; C_1206_3216Metric_Pad1.33x1.80mm_HandSolder
D1: SK33; D_SMC_Handsoldering
H1, H2, H3: MountingHole; MountingHole_3.2mm_M3
J1: Conn_01x02; Molex_KK-254_AE-6410-02A_1x02_P2.54mm_Vertical
J2, J3, J4: Conn_01x04; Molex_KK-254_AE-6410-04A_1x04_P2.54mm_Vertical
JP1, JP2, JP3: Jumper; PinHeader_1x02_P2.54mm_Vertical
L1: 330uH; L_12x12mm_H8mm; Part Number DE1209-330
U1: LM2575-3.3BT; TO-220-5_Vertical
U2: LM7805_TO220; TO-220-3_Vertical

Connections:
+3V3: J2.2, J3.2, J4.2, JP3.2 (B)
+5V: J2.3, J3.3, J4.3, JP2.2 (B)
+12V: C1.1, C2.1, C5.1, C6.1, J2.4, J3.4, J4.4, JP1.2 (B), U1.1 (VIN), U2.1 (VI)
GND: C1.2, C2.2, C3.2, C4.2, C5.2, C6.2, C7.2, D1.2 (A), J1.1, J2.1, J3.1, J4.1, U1.3 (GND), U1.5 (~ON/OFF), U2.2 (GND)
unnamed: D1.1 (K), L1.1, U1.2 (OUT)
unnamed: J1.2, JP1.1 (A)
unnamed: C7.1, JP2.1 (A), U2.3 (VO)
unnamed: C3.1, C4.1, JP3.1 (A), L1.2, U1.4 (FB)

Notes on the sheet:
Power board only needs the 12V rail, but there is no point in using a different connector

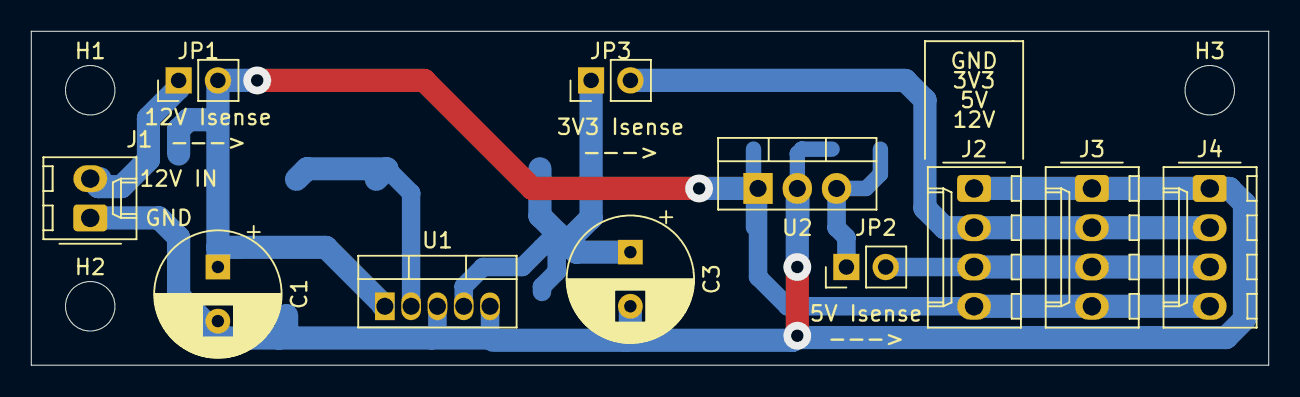
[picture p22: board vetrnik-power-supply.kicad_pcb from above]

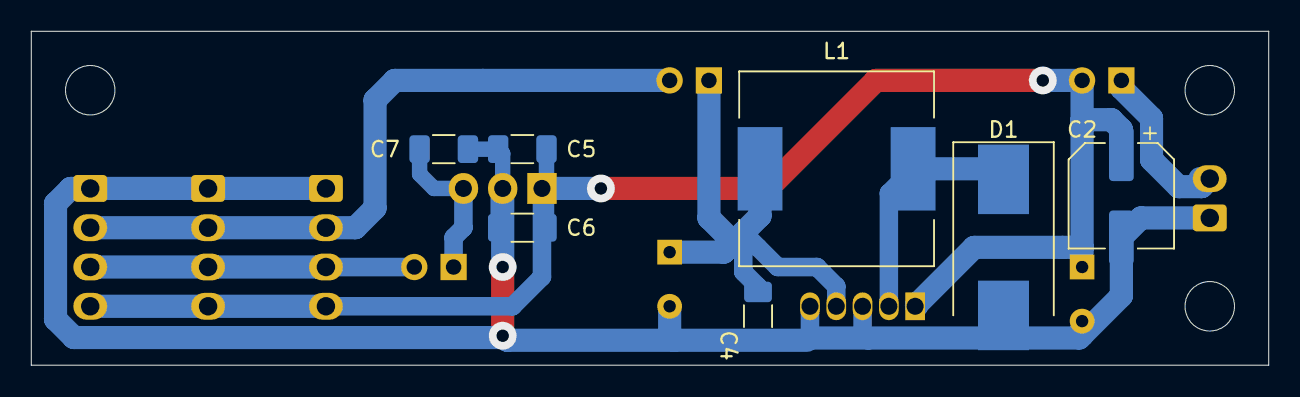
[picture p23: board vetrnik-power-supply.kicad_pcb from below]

Board: 2 copper layers, 80.0 x 21.6 mm, 21 parts (7 on the bottom side), 8 nets.

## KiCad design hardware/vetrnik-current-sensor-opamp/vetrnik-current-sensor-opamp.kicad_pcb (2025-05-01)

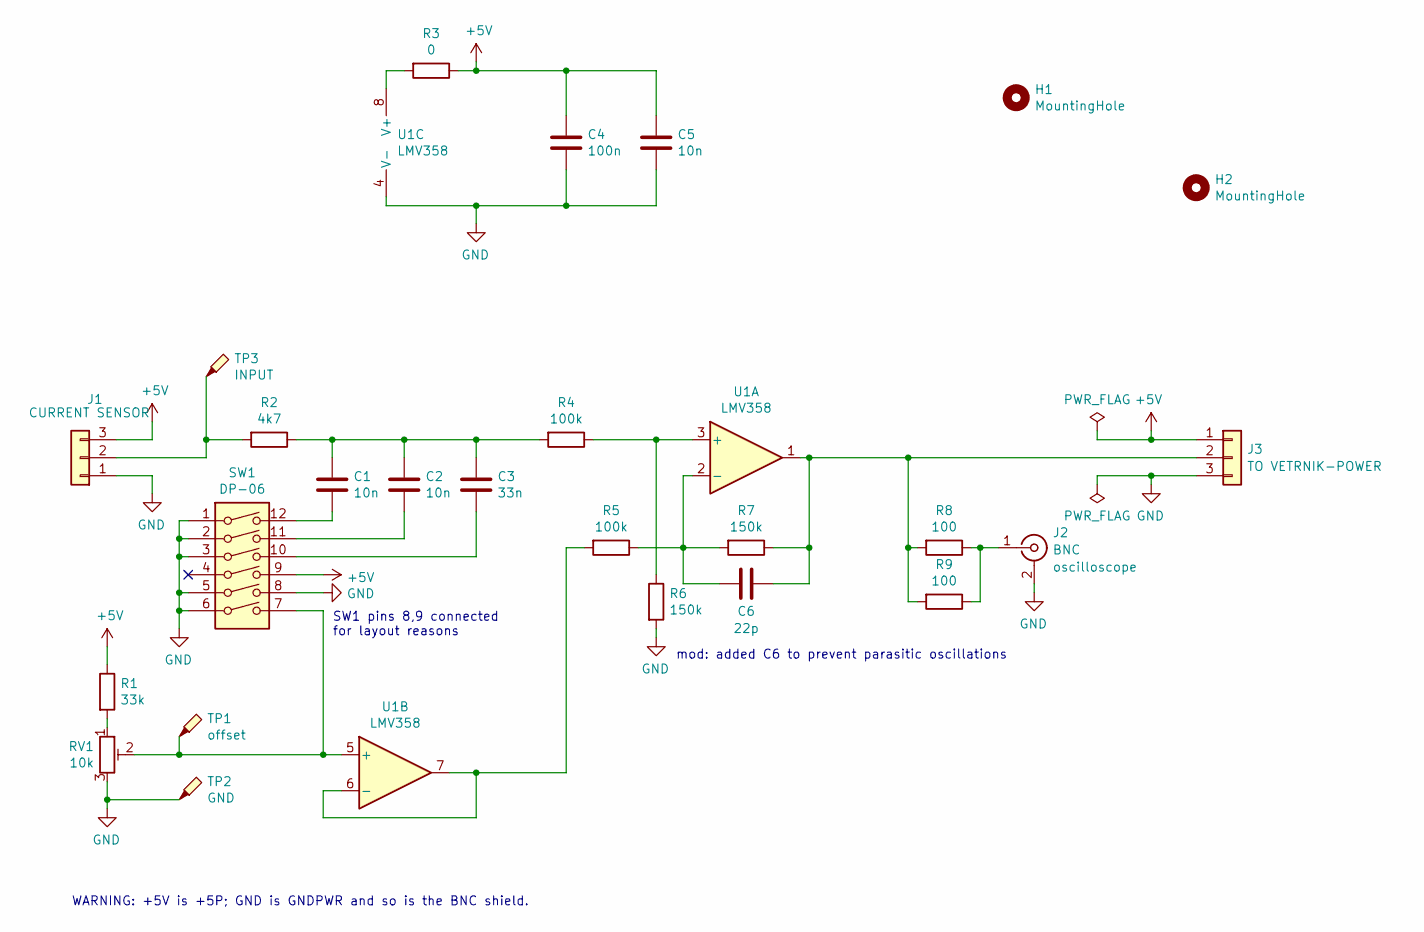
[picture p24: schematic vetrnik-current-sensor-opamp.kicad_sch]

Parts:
C1, C2, C5: 10n; C_1206_3216Metric_Pad1.33x1.80mm_HandSolder
C3: 33n; C_1206_3216Metric_Pad1.33x1.80mm_HandSolder
C4: 100n; C_1206_3216Metric_Pad1.33x1.80mm_HandSolder
C6: 22p
H1, H2: MountingHole; MountingHole_3.2mm_M3
J1, J3: Conn_01x03; Molex_KK-254_AE-6410-03A_1x03_P2.54mm_Vertical
J2: BNC; BNC_PanelMountable_Vertical
R1: 33k; R_1206_3216Metric_Pad1.30x1.75mm_HandSolder
R2: 4k7; R_1206_3216Metric_Pad1.30x1.75mm_HandSolder
R3: 0; R_1206_3216Metric_Pad1.30x1.75mm_HandSolder
R4, R5: 100k; R_1206_3216Metric_Pad1.30x1.75mm_HandSolder
R6, R7: 150k; R_1206_3216Metric_Pad1.30x1.75mm_HandSolder
R8, R9: 100; R_1206_3216Metric_Pad1.30x1.75mm_HandSolder
RV1: 10k; Potentiometer_Bourns_3296W_Vertical
SW1: DP-06; SW_DIP_SPSTx06_Piano_10.8x16.8mm_W7.62mm_P2.54mm
TP1: offset; PinSocket_1x01_P2.54mm_Vertical
TP2: GND; PinSocket_1x01_P2.54mm_Vertical
TP3: INPUT; PinSocket_1x01_P2.54mm_Vertical
U1: LMV358; SOIC-8_3.9x4.9mm_P1.27mm

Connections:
+5V: C4.1, C5.1, J1.3, J3.1, R1.1, R3.1, SW1.9
GND: C4.2, C5.2, J1.1, J2.2 (Ext), J3.3, R6.2, RV1.3, SW1.1, SW1.2, SW1.3, SW1.5, SW1.6, SW1.8, TP2.1, U1.4 (V-)
unnamed: C1.1, C2.1, C3.1, R2.1, R4.2
unnamed: C1.2, SW1.12
unnamed: C2.2, SW1.11
unnamed: C3.2, SW1.10
unnamed: J1.2, R2.2, TP3.1
unnamed: J2.1 (In), R8.1, R9.1
unnamed: C6.2, J3.2, R7.1, R8.2, R9.2, U1.1
unnamed: R1.2, RV1.1
unnamed: R3.2, U1.8 (V+)
unnamed: R4.1, R6.1, U1.3 (+)
unnamed: C6.1, R5.1, R7.2, U1.2 (-)
unnamed: R5.2, U1.6 (-), U1.7
unnamed: RV1.2, SW1.7, TP1.1, U1.5 (+)

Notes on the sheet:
WARNING: +5V is +5P; GND is GNDPWR and so is the BNC shield.
SW1 pins 8,9 connected for layout reasons
mod: added C6 to prevent parasitic oscillations

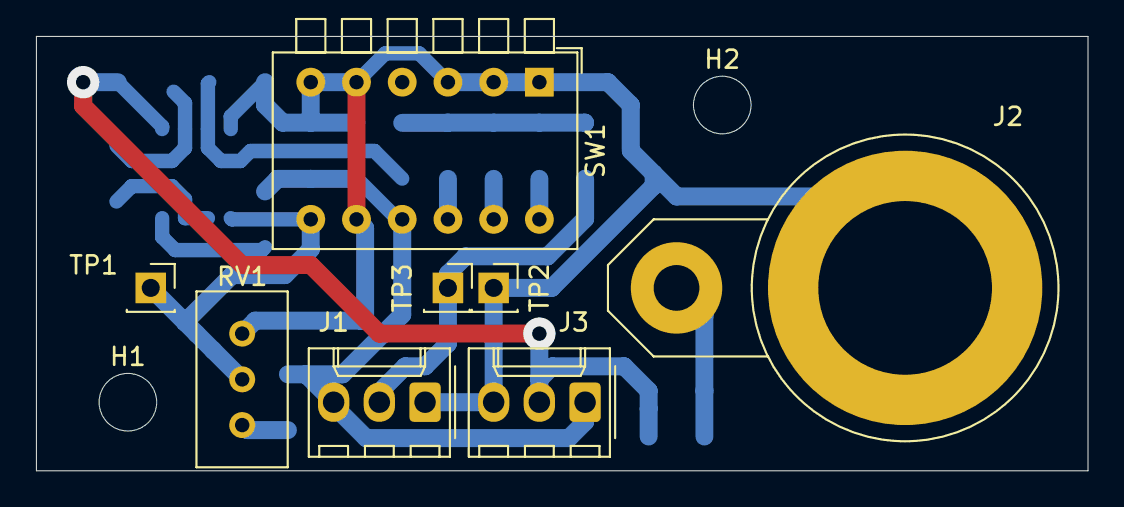
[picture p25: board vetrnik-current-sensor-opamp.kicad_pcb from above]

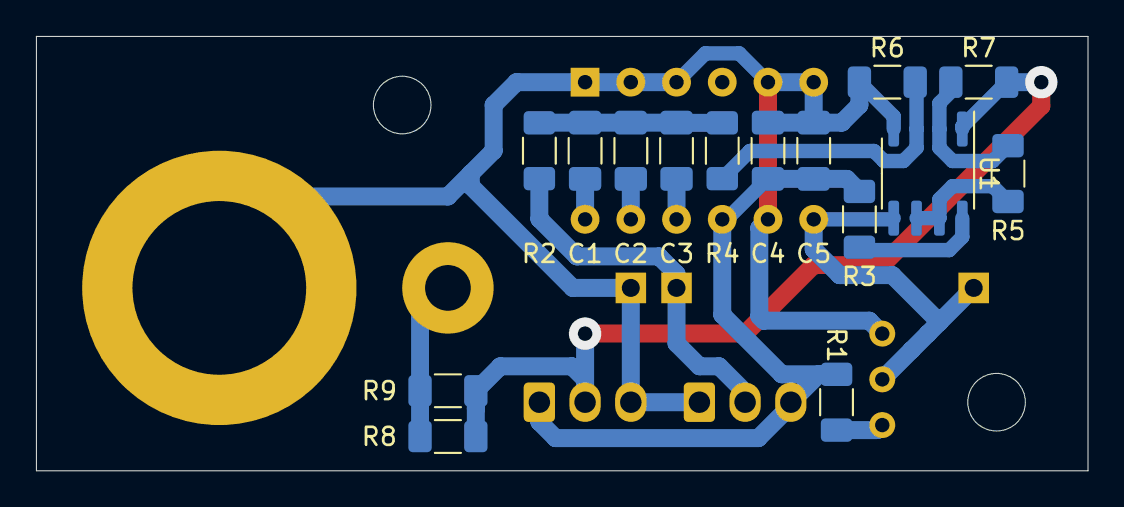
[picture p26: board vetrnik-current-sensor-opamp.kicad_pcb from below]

Board: 2 copper layers, 58.4 x 24.1 mm, 25 parts (15 on the bottom side), 15 nets.

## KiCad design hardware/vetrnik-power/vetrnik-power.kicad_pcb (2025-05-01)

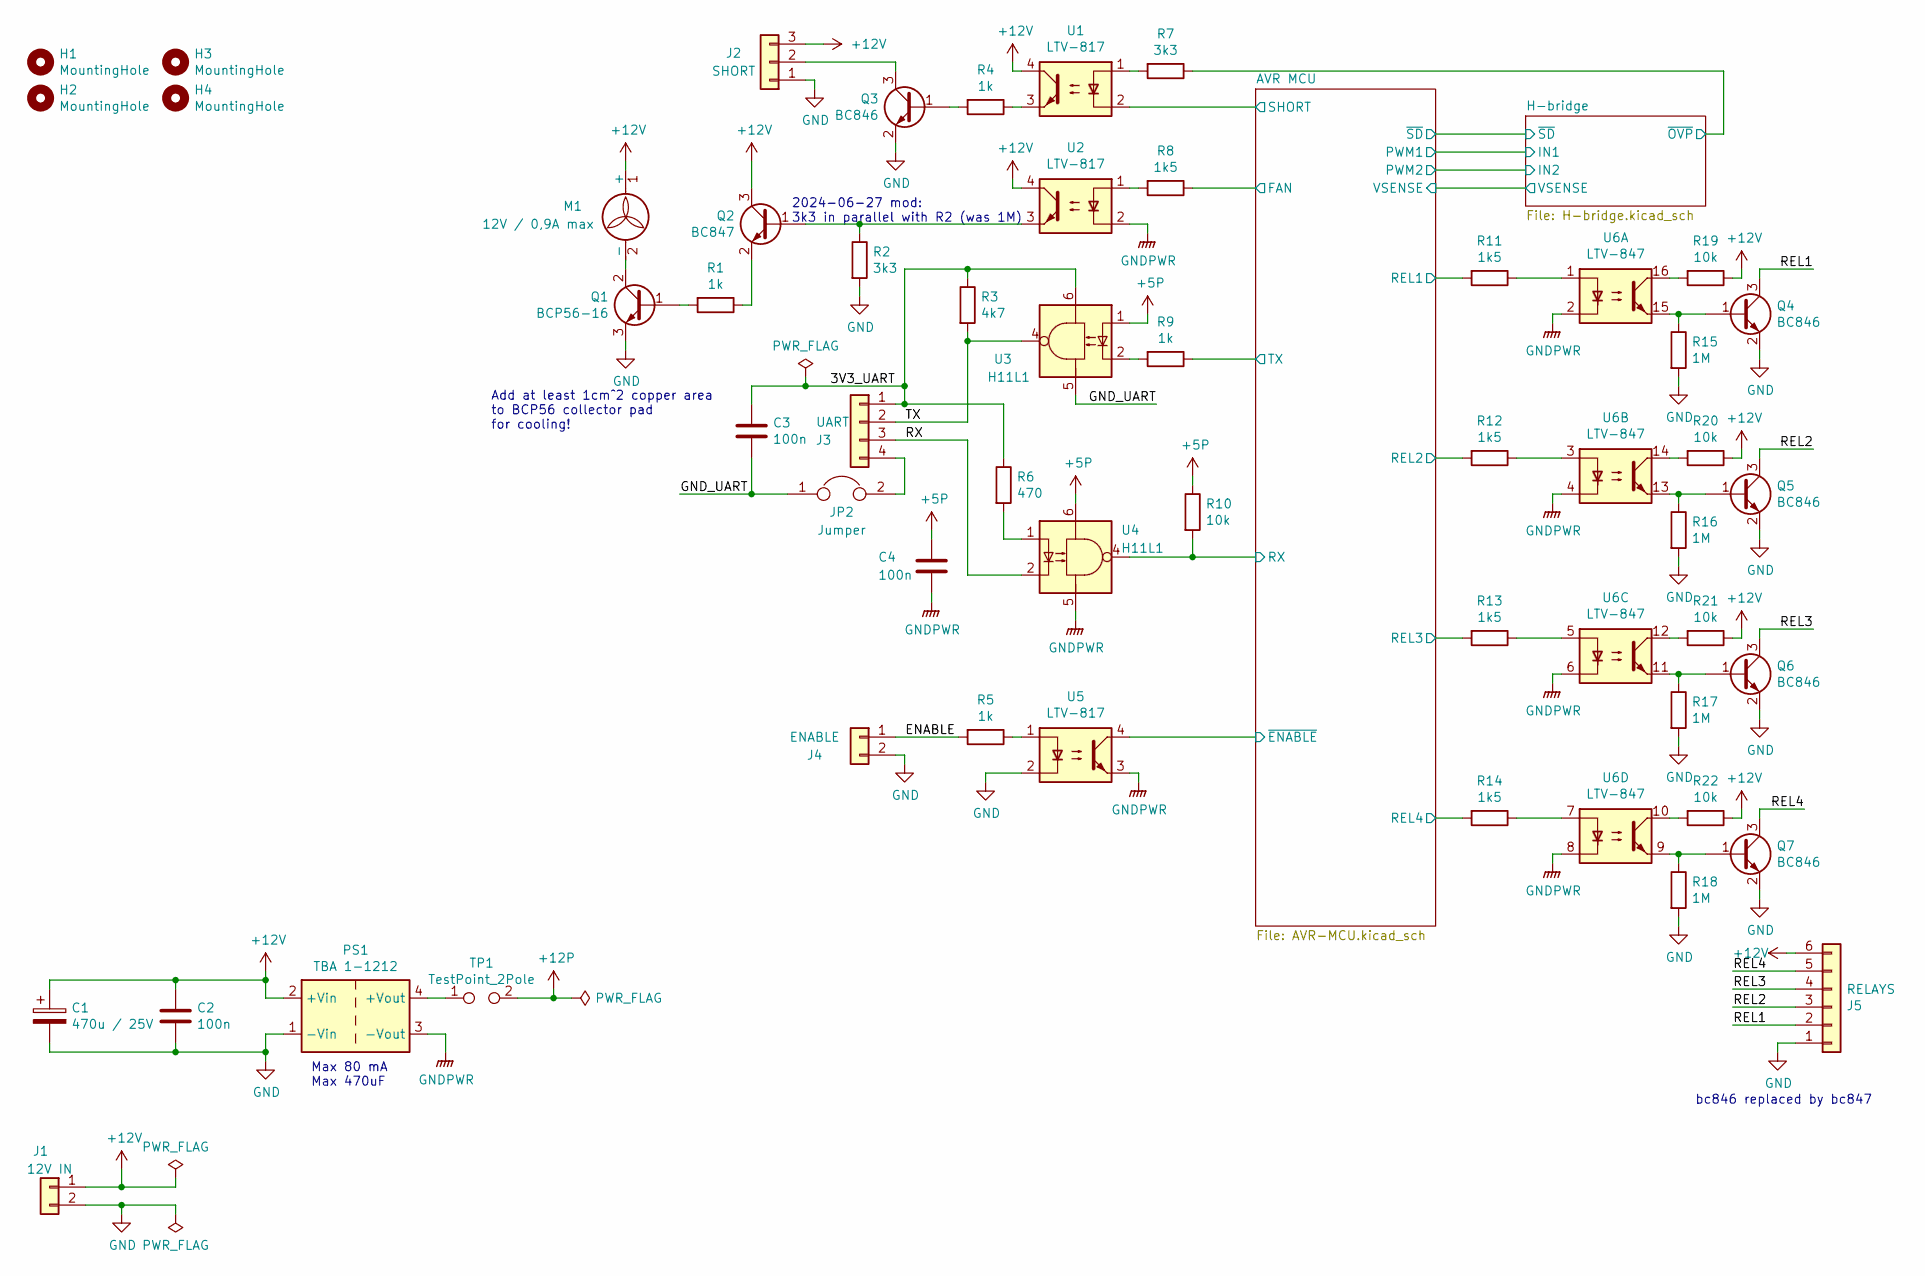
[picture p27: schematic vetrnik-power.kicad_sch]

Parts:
C1: 470u / 25V; CP_Radial_D10.0mm_P5.00mm
C2, C3, C4: 100n; C_1206_3216Metric_Pad1.33x1.80mm_HandSolder
H1, H2, H3, H4: MountingHole; MountingHole_3.2mm_M3
J1: 12V IN; Molex_KK-254_AE-6410-02A_1x02_P2.54mm_Vertical
J2: SHORT; Molex_KK-254_AE-6410-03A_1x03_P2.54mm_Vertical
J3: UART; Molex_KK-254_AE-6410-04A_1x04_P2.54mm_Vertical
J4: ENABLE; Molex_KK-254_AE-6410-02A_1x02_P2.54mm_Vertical
J5: RELAYS; Molex_KK-254_AE-6410-06A_1x06_P2.54mm_Vertical
JP2: Jumper; R_1206_3216Metric_Pad1.30x1.75mm_HandSolder
M1: 12V / 0,9A max; Molex_KK-254_AE-6410-02A_1x02_P2.54mm_Vertical
PS1: TBA 1-1212; Converter_DCDC_Murata_MEE1SxxxxSC_THT
Q1: BCP56-16; SOT-223-3_TabPin2
Q2: BC847; SOT-23
Q3, Q4, Q5, Q6, Q7: BC846; SOT-23
R1, R4, R5, R9: 1k; R_1206_3216Metric_Pad1.30x1.75mm_HandSolder
R2, R7: 3k3; R_1206_3216Metric_Pad1.30x1.75mm_HandSolder
R3: 4k7; R_1206_3216Metric_Pad1.30x1.75mm_HandSolder
R6: 470; R_1206_3216Metric_Pad1.30x1.75mm_HandSolder
R8, R11, R12, R13, R14: 1k5; R_1206_3216Metric_Pad1.30x1.75mm_HandSolder
R10, R19, R20, R21, R22: 10k; R_1206_3216Metric_Pad1.30x1.75mm_HandSolder
R15, R16, R17, R18: 1M; R_1206_3216Metric_Pad1.30x1.75mm_HandSolder
TP1: TestPoint_2Pole; PinHeader_1x02_P2.54mm_Vertical
U1, U2, U5: LTV-817; DIP-4_W7.62mm
U3, U4: H11L1; DIP-6_W7.62mm_LongPads
U6: LTV-847; DIP-16_W7.62mm

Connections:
+5P: C4.1, R10.1, U3.1, U4.6; also elsewhere on the board
+12P: TP1.2; also elsewhere on the board
+12V: C1.1, C2.1, J1.1, J2.3, J5.6, M1.1 (+), PS1.2 (+Vin), Q2.3 (C), R19.1, R20.1, R21.1, R22.1, U1.4, U2.4
/3V3_UART: C3.1, J3.1, R3.1, R6.1, U3.6
/AVR MCU/REL1: R11.2; also elsewhere on the board
/AVR MCU/REL2: R12.2; also elsewhere on the board
/AVR MCU/REL3: R13.2; also elsewhere on the board
/AVR MCU/REL4: R14.2; also elsewhere on the board
/AVR MCU/RX: R10.2, U4.4; also elsewhere on the board
/AVR MCU/SHORT: U1.2; also elsewhere on the board
/AVR MCU/TX: R9.1; also elsewhere on the board
/AVR MCU/~ENABLE: U5.4; also elsewhere on the board
/ENABLE: J4.1, R5.2
/GND_UART: C3.2, JP2.1, U3.5
/H-bridge/~OVP: R7.1; also elsewhere on the board
/REL1: J5.2, Q4.3 (C)
/REL2: J5.3, Q5.3 (C)
/REL3: J5.4, Q6.3 (C)
/REL4: J5.5, Q7.3 (C)
/RX: J3.3, U4.2
/TX: J3.2, R3.2, U3.4
GND: C1.2, C2.2, J1.2, J2.1, J4.2, J5.1, PS1.1 (-Vin), Q1.3 (E), Q3.2 (E), Q4.2 (E), Q5.2 (E), Q6.2 (E), Q7.2 (E), R2.2, R15.2, R16.2, R17.2, R18.2, U5.2
unnamed: J2.2, Q3.3 (C)
unnamed: J3.4, JP2.2
unnamed: M1.2 (-), Q1.2 (C), Q1.4 (C)
unnamed: PS1.4 (+Vout), TP1.1
unnamed: Q1.1 (B), R1.2
unnamed: Q2.1 (B), R2.1, U2.3
unnamed: Q2.2 (E), R1.1
unnamed: Q3.1 (B), R4.2
unnamed: Q4.1 (B), R15.1, U6.15
unnamed: Q5.1 (B), R16.1, U6.13
unnamed: Q6.1 (B), R17.1, U6.11
unnamed: Q7.1 (B), R18.1, U6.9
unnamed: R4.1, U1.3
unnamed: R5.1, U5.1
unnamed: R6.2, U4.1
unnamed: R7.2, U1.1
unnamed: R8.2, U2.1
unnamed: R9.2, U3.2
unnamed: R11.1, U6.1
unnamed: R12.1, U6.3
unnamed: R13.1, U6.5
unnamed: R14.1, U6.7
unnamed: R19.2, U6.16
unnamed: R20.2, U6.14
unnamed: R21.2, U6.12
unnamed: R22.2, U6.10

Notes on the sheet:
Add at least 1cm^2 copper area to BCP56 collector pad for cooling!
2024-06-27 mod: 3k3 in parallel with R2 (was 1M)
Max 80 mA Max 470uF
bc846 replaced by bc847

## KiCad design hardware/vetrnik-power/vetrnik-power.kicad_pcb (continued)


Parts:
C5, C10: 100n; C_1206_3216Metric_Pad1.33x1.80mm_HandSolder
C6, C7: 100n / 275VAC; C_Rect_L26.5mm_W10.5mm_P22.50mm_MKS4
C8, C9: 470u / 250V; CP_Radial_D30.0mm_P10.00mm_SnapIn
C11: 220u; CP_Radial_D8.0mm_P3.50mm
C12, C15: 22u / 35V; CP_Radial_D5.0mm_P2.00mm; not fitted
C13, C16: 1u / 25V; C_1206_3216Metric_Pad1.33x1.80mm_HandSolder; not fitted
C14: 15n / 300VAC; C_Rect_L18.0mm_W5.0mm_P15.00mm_FKS3_FKP3
C17: 220u; CP_Radial_D8.0mm_P3.50mm; not fitted
C18: 100n; C_1206_3216Metric_Pad1.33x1.80mm_HandSolder; not fitted
D1: 1.5KE150A; D_DO-201AE_P15.24mm_Horizontal
D2, D4: UF4004; D_DO-41_SOD81_P10.16mm_Horizontal; not fitted
D3: 1.5KE200CA; D_DO-201AE_P15.24mm_Horizontal
J6: DC IN; DG270-10.0-02P-14-00A
J7: PE; FS1536
J8: G #Q1; Molex_KK-254_AE-6410-02A_1x02_P2.54mm_Vertical
J9: G #Q2; Molex_KK-254_AE-6410-02A_1x02_P2.54mm_Vertical
J10: AC1; FS1536
J11: AC2; FS1536
J12: G #Q3; Molex_KK-254_AE-6410-02A_1x02_P2.54mm_Vertical
J13: G #Q4; Molex_KK-254_AE-6410-02A_1x02_P2.54mm_Vertical
NT1: Net-Tie_2; NetTie-2_SMD_Pad2.0mm
Q8: BC846; SOT-23
R23, R27: 100k / 0,6W; R_Axial_DIN0207_L6.3mm_D2.5mm_P10.16mm_Horizontal
R24, R28, R30: 3k3; R_1206_3216Metric_Pad1.30x1.75mm_HandSolder
R25, R29: 47k; R_1206_3216Metric_Pad1.30x1.75mm_HandSolder
R26, R49: 22k; R_1206_3216Metric_Pad1.30x1.75mm_HandSolder
R31, R32, R38: 10k; R_1206_3216Metric_Pad1.30x1.75mm_HandSolder; not fitted
R33, R34, R36, R37: 10; R_1206_3216Metric_Pad1.30x1.75mm_HandSolder; not fitted
R35: 10 / 0.5W; R_Axial_DIN0309_L9.0mm_D3.2mm_P12.70mm_Horizontal
U7: LM393; SOIC-8_3.9x4.9mm_P1.27mm
U8, U9: IR2104; SOIC-8_3.9x4.9mm_P1.27mm; not fitted

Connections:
+12P: C5.1, C10.1, C11.1, C17.1, C18.1, D2.2 (A), D4.2 (A), Q8.3 (C), R25.1, R30.1, U7.8 (V+), U8.1 (VCC), U9.1 (VCC); also elsewhere on the board
/AVR MCU/VSENSE: R23.2, R24.1; also elsewhere on the board
/AVR MCU/~SD: R31.1, U8.3 (~SD), U9.3 (~SD); also elsewhere on the board
/H-bridge/IN1: R32.1, U8.2 (IN); also elsewhere on the board
/H-bridge/IN2: R38.1, U9.2 (IN); also elsewhere on the board
/H-bridge/~OVP: Q8.2 (E); also elsewhere on the board
Earth: C6.2, C7.1, J7.1
unnamed: C12.1, C13.1, D2.1 (K), U8.8 (VB)
unnamed: C12.2, C13.2, J8.1, U8.6 (VS)
unnamed: C14.1, R35.2
unnamed: C14.2, D3.2 (A2), J10.1
unnamed: C15.1, C16.1, D4.1 (K), U9.8 (VB)
unnamed: C15.2, C16.2, J12.1, U9.6 (VS)
unnamed: D3.1 (A1), J11.1, R35.1
unnamed: J8.2, R33.1
unnamed: J9.2, R34.1
unnamed: J12.2, R36.2
unnamed: J13.2, R37.2
unnamed: Q8.1 (B), R29.1, R30.2, U7.1
unnamed: R25.2, R26.1, R29.2, R49.1, U7.3 (+)
unnamed: R27.2, R28.1, U7.2 (-)
unnamed: R33.2, U8.7 (HO)
unnamed: R34.2, U8.5 (LO)
unnamed: R36.1, U9.7 (HO)
unnamed: R37.1, U9.5 (LO)

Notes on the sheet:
2024-03 mod: added 5-pin connector for vetrnik-H-bridge: +12P, IN1, ~{SD}, IN2, GNDPWR. Components marked DNP (H-bridge drivers) moved to vetrnik-H-bridge.
+12P and GNDPWR are isolated from +12V and GND.
RefDes prefixed with # is a virtual symbol - off-board component
OVP should trip at 128V (standoff voltage of 1.5KE150A) See OVP-hysteresis.ods (128V ... 4.09V) 109V ... 3.49V 56V ... 1.79V WARNING: +12VP is UNREGULATED 12V!
mod: added R49 instead of making R26 10k


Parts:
C19, C21, C25, C26, C27, C31, C32: 100n; C_1206_3216Metric_Pad1.33x1.80mm_HandSolder
C20: 330n; C_1206_3216Metric_Pad1.33x1.80mm_HandSolder
C22, C23: 22p; C_1206_3216Metric_Pad1.33x1.80mm_HandSolder
C24: 1u / 25V; C_1206_3216Metric_Pad1.33x1.80mm_HandSolder
C28, C29, C30, C33, C34: 10n; C_1206_3216Metric_Pad1.33x1.80mm_HandSolder
D5: 1N4148W; D_SOD-123
D6: BAV99; SOT-23
J14: AC frequency sense; Molex_KK-254_AE-6410-02A_1x02_P2.54mm_Vertical
J15: AVR-ISP-6; IDC-Header_2x03_P2.54mm_Vertical
J16: NTC2; Molex_KK-254_AE-6410-03A_1x03_P2.54mm_Vertical
J17: ACS712; Molex_KK-254_AE-6410-03A_1x03_P2.54mm_Vertical
JP1: Jumper; R_1206_3216Metric_Pad1.30x1.75mm_HandSolder
Q9: BC847; SOT-23
Q10: BC846; SOT-23
R39: 330; R_1206_3216Metric_Pad1.30x1.75mm_HandSolder
R40: 22k 5W; R_Axial_DIN0922_L20.0mm_D9.0mm_P30.48mm_Horizontal
R41, R42, R44: 10k; R_1206_3216Metric_Pad1.30x1.75mm_HandSolder
R43: 100k; R_1206_3216Metric_Pad1.30x1.75mm_HandSolder
R45, R48: 4k7; R_1206_3216Metric_Pad1.30x1.75mm_HandSolder
R46: 47k; R_1206_3216Metric_Pad1.30x1.75mm_HandSolder
R47: 1k; R_1206_3216Metric_Pad1.30x1.75mm_HandSolder
SW1: AVR RESET; SW_PUSH_6mm_H4.3mm
TH1: TT7-10KC3-11; Molex_KK-254_AE-6410-02A_1x02_P2.54mm_Vertical
TP2: TestPoint_2Pole; PinHeader_1x02_P2.54mm_Vertical
U10: LTV-817; DIP-4_W7.62mm
U11: L78L05_TO92; TO-92L_HandSolder
U12: ATmega8-16PU; DIP-28_W7.62mm_Socket
Y1: 16MHz; Crystal_HC49-U_Vertical

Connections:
+5P: C21.1, C24.1, C31.1, C32.1, D6.2 (A), J15.2 (VCC), J16.1, J17.1, JP1.1, JP1.2, R41.1, R44.1, TH1.1, TP2.2, U10.4, U12.7 (VCC), U12.20 (AVCC); also elsewhere on the board
+12P: C20.1, U11.3 (VI); also elsewhere on the board
/AVR MCU/ADC0_VSENSE: C30.1, R47.1, U12.23 (PC0)
/AVR MCU/ADC1_ACS712: C29.1, J17.2, U12.24 (PC1)
/AVR MCU/ADC2_ACS712_2: C28.1, J16.2, R48.1, U12.25 (PC2)
/AVR MCU/ADC3_NTC1: C27.1, R45.1, TH1.2, U12.26 (PC3)
/AVR MCU/MISO: J15.1 (MISO), U12.18 (PB4)
/AVR MCU/REL1: U12.14 (PB0); also elsewhere on the board
/AVR MCU/REL2: U12.28 (PC5); also elsewhere on the board
/AVR MCU/REL3: U12.27 (PC4); also elsewhere on the board
/AVR MCU/REL4: J15.3 (SCK), U12.19 (PB5); also elsewhere on the board
/AVR MCU/RPM: C34.1, Q9.3 (C), R44.2, U12.4 (PD2), U12.6 (PD4)
/AVR MCU/RX: U12.2 (PD0); also elsewhere on the board
/AVR MCU/SHORT: Q10.3 (C); also elsewhere on the board
/AVR MCU/TX: U12.3 (PD1); also elsewhere on the board
/AVR MCU/VSENSE: D6.3 (K), R47.2; also elsewhere on the board
/AVR MCU/~ENABLE: U12.5 (PD3); also elsewhere on the board
/AVR MCU/~RST: C19.1, J15.5 (~RST), R39.1, R41.2, U12.1 (PC6/~RESET)
/AVR MCU/~SD: U12.13 (PD7); also elsewhere on the board
/AVR MCU/~SHORT: R46.2, U12.12 (PD6)
/H-bridge/IN1: U12.15 (PB1); also elsewhere on the board
/H-bridge/IN2: U12.16 (PB2); also elsewhere on the board
unnamed: C22.1, U12.9 (PB6/XTAL1), Y1.1
unnamed: C23.1, U12.10 (PB7/XTAL2), Y1.2
unnamed: C25.1, TP2.1, U11.1 (VO)
unnamed: C26.1, U12.21 (AREF)
unnamed: D5.1 (K), R40.1, U10.1
unnamed: D5.2 (A), J14.2, U10.2
unnamed: J14.1, R40.2
unnamed: C33.1, Q9.1 (B), R42.1, R43.1
unnamed: Q10.1 (B), R46.1
unnamed: R39.2, SW1.2
unnamed: R42.2, U10.3

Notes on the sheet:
mod: PD5 cannot do PWM on ATmega8 - connected to PB3
C33 didn't help for noise filtering, Ihad to install C34 (both are bodged in THT caps at the bottom side of the board)
TP2 is a test point for current measurement; normally jumpered across.
PD2, PD3 are INT0 & INT1
PD4, PD5 timer inputs
2023-03-04 mod: added R48, J16 is now an NTC channel.
ACS712 takes 13 mA from isolated supply!

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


Board: 2 copper layers, 124.5 x 99.1 mm, 138 parts (83 on the bottom side), 95 nets.

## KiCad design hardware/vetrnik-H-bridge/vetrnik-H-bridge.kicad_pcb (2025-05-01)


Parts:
C1: 220u / 25V; CP_Elec_8x10
C2, C3, C8, C9: 10u / 25V; C_1206_3216Metric_Pad1.33x1.80mm_HandSolder
C4, C5: 100n; C_1206_3216Metric_Pad1.33x1.80mm_HandSolder
C6, C7: 10n; C_1206_3216Metric_Pad1.33x1.80mm_HandSolder
C10, C11: 10u / 25V; C_1206_3216Metric_Pad1.33x1.80mm_HandSolder; not fitted
D1, D2, D3: ESD5Z5V0; D_SOD-523
D4, D5: LED; LED_1206_3216Metric_Pad1.42x1.75mm_HandSolder
D6, D7: SUF4004; D_MELF_Handsoldering
D8, D9, D10, D11: SMAJ13A; D_SMA
D12, D13, D14, D15: DNP 1N4148W; D_SOD-123; not fitted
H1, H2, H3, H4: MountingHole; MountingHole_3.2mm_M3
J1: Conn_01x05; SolderWire-0.25sqmm_1x05_P4.2mm_D0.65mm_OD1.7mm_Relief
J2, J3, J4, J5: Conn_01x02_Pin; SolderWire-0.15sqmm_1x02_P4mm_D0.5mm_OD1.5mm_Relief
R1: 0; R_1206_3216Metric_Pad1.30x1.75mm_HandSolder
R2, R3, R4: 1k; R_1206_3216Metric_Pad1.30x1.75mm_HandSolder
R5, R6, R7, R18, R19, R20, R21: 22k; R_1206_3216Metric_Pad1.30x1.75mm_HandSolder
R8, R9: 10k / 1.5W; R_2512_6332Metric_Pad1.40x3.35mm_HandSolder
R10, R11, R12, R13, R14, R15, R16, R17: 10; R_1206_3216Metric_Pad1.30x1.75mm_HandSolder
U1, U2: IR2104; SOIC-8_3.9x4.9mm_P1.27mm

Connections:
+12P: C1.1, C2.1, C3.1, C4.1, C5.1, C6.1, C7.1, D6.2 (A), D7.2 (A), J1.5, U1.1 (VCC), U2.1 (VCC)
/AC1: C8.2, C10.2, D8.2 (A2), J2.1, R8.1, R18.2, U1.6 (VS)
/AC2: C9.2, C11.2, D10.2 (A2), J4.1, R9.1, R20.2, U2.6 (VS)
/CONN_IN1: D1.1 (K), J1.4, R2.2
/CONN_IN2: D3.1 (K), J1.2, R4.2
/CONN_~SD: D2.1 (K), J1.3, R3.2
/IN1: R2.1, R5.1, U1.2 (IN)
/IN2: R4.1, R7.1, U2.2 (IN)
/~SD: R3.1, R6.1, U1.3 (~SD), U2.3 (~SD)
GNDPWR: C1.2, C2.2, C3.2, C4.2, C5.2, C6.2, C7.2, D9.2 (A2), D11.2 (A2), J3.1, J5.1, R1.2, R5.2, R6.2, R7.2, R19.2, R21.2, U1.4 (COM), U2.4 (COM)
unnamed: D1.2 (A), D2.2 (A), D3.2 (A), J1.1, R1.1
unnamed: D4.2 (A), D5.1 (K), R8.2
unnamed: D4.1 (K), D5.2 (A), R9.2
unnamed: C8.1, C10.1, D6.1 (K), U1.8 (VB)
unnamed: C9.1, C11.1, D7.1 (K), U2.8 (VB)
unnamed: D10.1 (A1), D14.1 (K), R12.2, R16.1
unnamed: D11.1 (A1), D15.1 (K), R13.2, R17.1
unnamed: D12.2 (A), J2.2, R14.2, R18.1
unnamed: D8.1 (A1), D12.1 (K), R10.2, R14.1
unnamed: D13.2 (A), J3.2, R15.2, R19.1
unnamed: D9.1 (A1), D13.1 (K), R11.2, R15.1
unnamed: D14.2 (A), J4.2, R16.2, R20.1
unnamed: D15.2 (A), J5.2, R17.2, R21.1
unnamed: R10.1, U1.7 (HO)
unnamed: R11.1, U1.5 (LO)
unnamed: R12.1, U2.7 (HO)
unnamed: R13.1, U2.5 (LO)

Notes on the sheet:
LEDs might help detect shorted transistors (although if one is shorted & the other is on, it will form a voltage divider) 200V/20kOhm = 10mA ; 2W 10V/20kohm = 0.5mA Both LEDs need to be the same color to get comparable brightness.
I will have to leave one of the 220uF caps on vetrnik-power and the isolated power supply only allows 470uF output cap. The other 220uF on vetrnik-power has to be removed!
TBA 1-1212 in vetrnik-power (source of +12P) has unregulated output, can be 10% higher than its input. SMAJ12A has Vbrmin = 13.3 --> 13.3/1.1 = 12.09V maximum input to DC-DC SMAJ13A has Vbrmin = 14.4 --> 14.4/1.1 = 13.09V maximum input to DC-DC --> SMAJ13A is better, but clamping voltage of 21.5V i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


Board: 2 copper layers, 57.8 x 61.0 mm, 58 parts (0 on the bottom side), 27 nets.

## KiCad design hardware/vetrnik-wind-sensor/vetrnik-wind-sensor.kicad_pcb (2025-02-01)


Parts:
C1, C8: RAD 1000/10 HT RM5; CP_Radial_D8.0mm_P5.00mm; Rated Voltage 10V
C2: RAD 470/25 HT RM5; CP_Radial_D10.0mm_P5.00mm; Rated Voltage 25V
C3: 1u / 25V; C_1206_3216Metric_Pad1.33x1.80mm_HandSolder
C4: 10u / 25V; C_1206_3216Metric_Pad1.33x1.80mm_HandSolder
C5, C7, C9: 100n; C_1206_3216Metric_Pad1.33x1.80mm_HandSolder
C6: 10u / 50V; C_1206_3216Metric_Pad1.33x1.80mm_HandSolder
D1: ESD5Z5V0; D_SOD-523; Breakdown Voltage 6.2V; Forward Voltage 6.2V
D2: SM712-02HTG; SOT-23; Breakdown Voltage 7.5...13.3V; Forward Voltage 7.5...13.3V
D3: SMAJ28A-13-F; D_SMA_Handsoldering; Breakdown Voltage 31.1...34.4V; Forward Voltage 31.1...34.4V
F1: 0ZCJ0025AF2E; Fuse_1206_3216Metric_Pad1.42x1.75mm_HandSolder; Rated Voltage 24V
H1, H2, H4: MountingHole; MountingHole_3.2mm_M3
H3: MountingHole_Pad; MountingHole_3.2mm_M3_Pad
J1, J2: NS25-W4P; Molex_KK-254_AE-6410-04A_1x04_P2.54mm_Vertical; Rated Voltage 0.25kV
J3: Conn_01x08; PinHeader_1x08_P2.54mm_Vertical
J4: MTJ-88GX1-FSD; RJ45_HALO_HFJ11-x2450HRL_Horizontal
JP1: SolderJumper_2_Bridged; R_1206_3216Metric_Pad1.30x1.75mm_HandSolder
NT1, NT2: NetTie_2; R_1206_3216Metric_Pad1.30x1.75mm_HandSolder
R1, R3, R9, R11: 470; R_1206_3216Metric_Pad1.30x1.75mm_HandSolder
R2: 4k7; R_1206_3216Metric_Pad1.30x1.75mm_HandSolder
R4, R5: 10k; R_1206_3216Metric_Pad1.30x1.75mm_HandSolder
R6: 1k; R_1206_3216Metric_Pad1.30x1.75mm_HandSolder
R7, R8: 10; R_1206_3216Metric_Pad1.30x1.75mm_HandSolder
R10: 150 / 0.25W; R_1206_3216Metric_Pad1.30x1.75mm_HandSolder
U1: AM1D-1224SH30Z; Converter_DCDC_TRACO_TEA1-xxxxHI_THT; Input Voltage 10.8...13.2V DC; Output Voltage 24V DC
U2: RYK-0505S/H; Converter_DCDC_TRACO_TEA1-xxxxHI_THT; Input Voltage 5V DC; Output Voltage 5V DC
U3, U4, U5: H11L1S(TA); SMDIP-6_W9.53mm
U6: THVD1400DR; SOIC-8_3.9x4.9mm_P1.27mm; Supply Voltage 3...5.5V DC

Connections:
+3V3: C5.1, J2.2, R2.1, U3.1, U4.1, U5.6
+5P: C7.1, C8.1, C9.1, D1.1 (K), R4.1, R5.1, R9.1, U2.7 (+Vout), U3.6, U4.6, U5.1, U6.8 (VCC)
+5V: C1.1, C4.1, J2.3, U2.1 (+Vin)
+12V: F1.1, J2.4
+24V: C6.1, D3.1 (K), J3.7, J4.7, U1.7 (+Vout)
/DE: J1.3, R1.1
/MODBUS_A: D2.1 (A1), J3.5, J4.5, R7.2, R9.2, R10.1
/MODBUS_B: D2.2 (A2), J3.4, J4.4, R8.2, R10.2, R11.1
/RX: J1.1, R2.2, U5.4
/TX: J1.2, R3.1
Earth: H3.1, J4.SH, JP1.2 (B)
GND: C1.2, C2.2, C3.2, C4.2, C5.2, J1.4, J2.1, U1.2 (-Vin), U2.2 (-Vin), U5.5
GNDPWR: C6.2, C7.2, C8.2, C9.2, D1.2 (A), D2.3 (common), D3.2 (A), J3.8, J4.8, JP1.1 (A), R11.2, U1.5 (-Vout), U2.5 (-Vout), U3.5, U4.5, U6.5 (GND)
unnamed: J3.1, J4.1
unnamed: J3.2, J4.2
unnamed: J3.3, J4.3
unnamed: J3.6, J4.6
unnamed: NT1.1, R1.2
unnamed: NT1.2, U3.2
unnamed: NT2.1, R4.2, U3.4
unnamed: R3.2, U4.2
unnamed: R6.1, U5.2
unnamed: C2.1, C3.1, F1.2, U1.1 (+Vin)
unnamed: R7.1, U6.6 (A)
unnamed: R8.1, U6.7 (B)
unnamed: NT2.2, U6.2 (~RE), U6.3 (DE)
unnamed: R5.2, U4.4, U6.4 (DI)
unnamed: R6.2, U6.1 (RO)

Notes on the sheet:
Sensor current < 15mA (specified <= 0.3W) 28V TVS -> up to 16% out-of-spec 24V allowed. DC-DC Vout accuracy is +-3% & 1.2% Vout / 1% Vin
RYK-0505S/H is regulated 5V/5V with 0% minimum load ; 200 mA max AM1D-1224SH30Z: 12/24V unregulated, min load unspecified
Mounting holes: M3 20x75 mm
220 uF max - sensor does not specify input capacitance!



Board: 2 copper layers, 99.7 x 31.8 mm, 41 parts (28 on the bottom side), 28 nets.

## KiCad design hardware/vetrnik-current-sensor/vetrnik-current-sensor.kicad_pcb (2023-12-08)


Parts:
C1: 100n; C_1206_3216Metric_Pad1.33x1.80mm_HandSolder
H1, H2, H3, H4: MountingHole; MountingHole_3.2mm_M3
J1: DG270-10.0-02P; DG270-10.0-02P-14-00A
J2: Conn_01x03; Molex_KK-254_AE-6410-03A_1x03_P2.54mm_Vertical
U1: ACS770xCB-050U-PFF; Allegro_CB_PFF

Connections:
+5V: C1.1, J2.3, U1.1 (VCC)
GND: C1.2, J2.2, U1.2 (GND)
unnamed: J1.1, U1.4 (IP+)
unnamed: J1.2, U1.5 (IP-)
unnamed: J2.1, U1.3 (VIOUT)


Board: 2 copper layers, 50.8 x 59.7 mm, 8 parts (1 on the bottom side), 5 nets.

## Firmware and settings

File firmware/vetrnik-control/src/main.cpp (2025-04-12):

#include <Arduino.h>
#include "settings.h"

#ifdef WATCHDOG_TIME
#include <IWatchdog.h>
#endif

#include "uart_power.h"
#include "power_datapoints.h"
#include "mqtt.h"
#include "ota.h"
#include "cli.h"
#include "debug.h"
#include "power_board.h"
#include "lisp.h"
#include "control.h"
#include "stats.h"
#include "display.h"
#include "sensor_DS18B20.h"
#include "sensor_wind.h"
#include "log.h"
#include "reset_cause.h"
#include <SerialFlash.h>
#include <Bounce2.h>


static Bounce2::Button button1 = Bounce2::Button();
static Bounce2::Button button2 = Bounce2::Button();


void setup()
{
    reset_cause_t reset_cause = reset_cause_get();
    log_init(
        reset_cause == RESET_CAUSE_BROWNOUT_RESET ||
        reset_cause == RESET_CAUSE_POWER_ON_POWER_DOWN_RESET
    );
    log_add_record_reboot(reset_cause);

    Serial.begin();
    log_add_INFO_backend(&Serial);

    button1.attach(PIN_BUTTON1, INPUT_PULLUP);
    button1.interval(BUTTON_DEBOUNCE);
    button1.setPressedState(LOW);
    button2.attach(PIN_BUTTON2, INPUT_PULLUP);
    button2.interval(BUTTON_DEBOUNCE);
    button2.setPressedState(LOW);

    pinMode(PIN_CONTACTOR_SENSE, INPUT_PULLUP);
    pinMode(PIN_BUZZER, OUTPUT);
    pinMode(PIN_EMERGENCY, OUTPUT);
    pinMode(PIN_LED, OUTPUT);
    // PIN_ONEWIRE is unused
    pinMode(PIN_REL1, OUTPUT);
    pinMode(PIN_REL2, OUTPUT);

    pinMode(PIN_ETH_RST, OUTPUT);
    ETH_reset();

    digitalWrite(PIN_BUZZER, HIGH);
    pinMode(LED_BUILTIN, OUTPUT);
    for (uint8_t i = 0; i < 4; i++)
    {
        digitalWrite(LED_BUILTIN, LOW);
        delay(100);
        digitalWrite(LED_BUILTIN, HIGH);
        delay(100);
    }
    INFO->print("Flash init: ");
    INFO->println(SerialFlash.begin(PIN_FLASH_SS));
    INFO->println("settings_init");
    INFO->flush();
    settings_init();
    INFO->flush();
    MQTT_init();
#ifdef WATCHDOG_TIME
    // Only do this after MQTT_init (DHCP is slow)
    IWatchdog.begin(WATCHDOG_TIME*1000UL);
#endif
    uart_power_init();
    control_init();
    sensor_DS18B20_init();
    sensor_wind_init();
    lisp_init();
    INFO->println("boot");
    CLI_init();
    display_init();
    lisp_run_blind_file(LISP_INIT_FILENAME, -1);

    digitalWrite(PIN_BUZZER, LOW);
}


void loop()
{
    unsigned long loop_start_millis = millis();
    button1.update();
    if (button1.released())
    {
        if (button1.previousDuration() < BUTTON_LONG)
        {
            lisp_run_blind("(btn1_short)");
        }
        else if (button1.previousDuration() >= BUTTON_LONG)
        {
            lisp_run_blind("(btn1_long)");
        }
    }
    button2.update();
    if (button2.released())
    {
        if (button2.previousDuration() < BUTTON_LONG)
        {
            lisp_run_blind("(btn2_short)");
        }
        else if (button2.previousDuration() >= BUTTON_LONG)
        {
            lisp_run_blind("(btn2_long)");
        }
    }

    power_datapoints_loop();
    bool status_complete = uart_power_loop();
    if (status_complete)
    {
        power_board_status = power_board_status_read();
        control_new_state();
        stats_new_state();
        static bool prev_emergency = false;
        if (power_board_status.emergency != prev_emergency)
        {
            prev_emergency = power_board_status.emergency;
            log_add_event(kPowerBoardEmergency);
        }
    }
    else if (power_board_status.valid &&
             millis() - power_board_status.retrieved_millis >= 2000UL)
    {
        log_add_event_and_println(kPowerBoardStatusTimeout, INFO);
        power_board_status.valid = false;
        control_new_state();
        stats_new_state();
    }

    sensor_DS18B20_loop();
    sensor_wind_loop();
    control_loop();
    CLI_loop();
    unsigned long loop_duration_mid = millis() - loop_start_millis;
    MQTT_loop();
    ota_loop();
    display_loop();

    unsigned long now = millis();
    unsigned long loop_duration = now - loop_start_millis;
    if (loop_duration >= 1500U)
    {
        log_add_record_slow_loop(loop_duration, loop_duration_mid);
    }

    // detect & log millis rollover
    static unsigned long rollover_prev_millis = 0;
    if (now < rollover_prev_millis)
    {
        log_add_event(kMillisRollover);
    }
    rollover_prev_millis = now;

    log_update_lastms();


#ifdef WATCHDOG_TIME
    IWatchdog.reload();
#endif
}

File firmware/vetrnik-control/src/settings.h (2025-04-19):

#pragma once
#include <stdint.h>

#define PIN_FLASH_SS    PB1
#define PIN_BUZZER      PB12
#define PIN_BUTTON1     PB13
#define PIN_BUTTON2     PB14
#define PIN_EMERGENCY   PB15 // emergency contactor control; low = emergency mode
#define PIN_LED         PA15
#define PIN_ONEWIRE     PB5
#define PIN_REL1        PB8
#define PIN_REL2        PB9
#define PIN_NTC1        PA0  // ADC
#define PIN_NTC2        PA1  // ADC
#define PIN_ETH_RST     PB10 // active low
#define PIN_CONTACTOR_SENSE PC14  // low = emergency mode

#define PIN_WIND_DE     PB0
#define UART_WIND       Serial2  // PA2, PA3

#define BUTTON_DEBOUNCE 50  // ms
#define BUTTON_LONG 500  // ms

#define LISP_INIT_FILENAME "init.lisp"

#define MQTTport 1883
#define MQTTclientID "vetrnik"  // TODO make this a conf option
#define MQTTReconnectRate 20*1000UL  // in ms
#define MQTTWaitBeforeReconnect 5*1000UL  // in ms
#define MQTTWaitBeforeEthernetReset 15*60000UL  // in ms
#define MQTTtopic_prefix                    "vetrnik/"
#define MQTTtopic_tele                      MQTTtopic_prefix "tele/"
#define MQTTtopic_cmnd                      MQTTtopic_prefix "cmnd/"
#define MQTTtopic_stat                      MQTTtopic_prefix "stat/"
#define MQTTtopic_availability              MQTTtopic_tele "availability"

#define MQTTtopic_tele_raw_RX               MQTTtopic_tele "raw/RX/"
#define MQTTtopic_tele_power_board          MQTTtopic_tele "power_board/"
#define MQTTtopic_tele_control              MQTTtopic_tele "control/"
#define MQTTtopic_tele_stats                MQTTtopic_tele "stats/"
#define MQTTtopic_tele_temperature          MQTTtopic_tele "temperature/"

#define WATCHDOG_TIME 16000UL  // WDT is only used if this is defined
#define SHELL_TELNET

#define SENSOR_DS18B20_COUNT 10
/// How many retries --> the temperature is read SENSOR_DS18B20_RETRIES+1 times.
#define SENSOR_DS18B20_RETRIES 2

#define SETTINGS_FILENAME "settings"

// X(const_name, error_message)
#define SETTINGS_ERRORS(X) \
    X(OK, "OK") \
    X(MISSING_OPTION, "Missing option") \
    X(INVALID_OPTION, "Invalid conf option") \
    X(MISSING_VALUE, "Missing value") \
    X(INVALID_IP, "Invalid format, expected d.d.d.d") \
    X(INVALID_MAC, "Invalid format, expected xx:xx:xx:xx:xx:xx") \
    X(STR_TOO_LONG, "String too long") \
    X(INVALID_UINT8, "Value not in range 0-255") \
    X(INVALID_DS18B20, "Bad format") \
    X(INVALID_DS18B20_ID, "Bad id")

#define X_ENUM(const_name, error_message) SETTINGS_E_##const_name,
typedef enum {
    SETTINGS_ERRORS(X_ENUM)
} settings_parse_error_t;
#undef X_ENUM


typedef struct {
    uint8_t address[8];
    char name[16];
} settings_DS18B20_t;


#define COMMA ,
// X(printer_name, data_type, array_len?, name, default_value)
// array_len: '[array_length]' || ':number_of_bits' || ''
// cppcheck-suppress preprocessorErrorDirective
#define CONF_ITEMS(X) \
    /* printer data    arr     name                 default */ \
    X(MAC,  uint8_t,  [6],    ETH_MAC,              { 0xDE COMMA 0xAD COMMA 0xBE COMMA 0xEF COMMA 0xFE COMMA 0xED }) \
    X(IP,   uint8_t,  [4],    ETH_IP,               {0}) /* IPv4 */ \
    X(IP,   uint8_t,  [4],    MQTTserver,           {0}) /* IPv4 */ \
    X(str,  char,     [16],   MQTTuser,             "") \
    X(str,  char,     [32],   MQTTpassword,         "") \
    X(int,  uint8_t,  ,       DS18B20_sampling,     10) /* seconds, no sampling if 0 */ \
    X(DS18B20, settings_DS18B20_t, [SENSOR_DS18B20_COUNT], DS18B20s, {0}) /* default: all zeros */ \
    X(str,  char,     [16],   OTAname,              "vetrnik") /* probably for mDNS, untested */ \
    X(str,  char,     [32],   OTApassword,          "pass") \
    X(bool, bool,     :1,     shell_telnet,         true) /* important: default true to prevent lockout */ \
    X(bool, bool,     :1,     report_raw,           false) /* MQTT report of raw datapoints */ \
    X(int,  uint8_t,  ,       contactor_debounce_min, 15) \
    X(int,  uint8_t,  ,       DHCP_timeout_s,       14) /* default timeout in Ethernet.h is 60 s ; needs to be lower than WATCHDOG_TIME */ \
    X(int,  uint8_t,  ,       MQTT_timeout_s,       4) /* default timeout is 15 s, should be lower than power board uart timeout (5.1s) */ \
    X(int,  uint8_t,  ,       wind_sampling,        5) /* *100 ms, no sampling if 0 */ \
    /* */


// #undef COMMA - cannot undef, needed during expansion

#define X_STRUCT(printer, type, arr, name, default) type name arr;

typedef struct {
    CONF_ITEMS(X_STRUCT)
} settings_t;

#undef X_STRUCT

extern settings_t settings;
extern const settings_t settings_default;


settings_parse_error_t settings_parse(char * line, settings_t * s);
const char * settings_parse_error_message(settings_parse_error_t);
void settings_init();
void settings_write(const settings_t & s);
void settings_print(const settings_t * s, void(print_line)(void*, char *), void* ctx, bool conf_prefix);

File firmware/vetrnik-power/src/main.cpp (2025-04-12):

#include <Arduino.h>
#include <avr/wdt.h>
#include <avr/eeprom.h>

#include <serial.h>
#include "hardware.h"
#include "uart.h"
#include "Hbridge.h"
#include "RPM.h"
#include "adc.h"
#include "globals.h"
#include "settings.h"

#include <errm.h>
const byte ERRM_COUNT_MAX=5;
errm_error errm_errors[ERRM_COUNT_MAX];
void error_create_callback(const errm_error *err);
#include "error_templates.h"


static unsigned long mode_prev_millis = 0;
static uint8_t stopping_duty = 0;

bool set_mode(mode_t new_mode)
{
    if (emergency) return false;
    switch (new_mode)
    {
        case mode_emergency:
            gpio_clr(pin_EMERGENCY);  // active low
            Hbridge_set_enabled(false);
            mode = mode_emergency;
            break;

        case mode_stopping:
            {
                if (mode != mode_const_duty) return false;
                stopping_duty = duty;
                // Not overwriting duty to be able to recover after enable input
                // goes back up.
                mode_prev_millis = millis();
            }
            mode = mode_stopping;
            break;

        case mode_const_duty:
            {
                if (mode != mode_stopping) return false;
                if (OVP_stop) return false;  // prevent is_enabled() logic from fighting OVP stop
                // Stopping mode can sometimes activate the emergency contactor
                // if it detects it is not effective by itself.
                gpio_set(pin_EMERGENCY);
                Hbridge_set_duty(duty);
            }
            mode = mode_const_duty;
            break;

        case mode_start:
            {
                if (mode != mode_emergency) return false;
                if (emergency) return false;
                Hbridge_set_duty(0);
                duty = 0;
                Hbridge_set_enabled(true);
                gpio_set(pin_EMERGENCY);
            }
            mode = mode_const_duty;
            break;
    }
    return true;
}


void error_create_callback(const errm_error *err)
{
    if (err->errortemplate->weight >= 10 && !emergency)
    {
        emergency_stop();
    }
}


// See avr/wdt.h
// https://www.avrfreaks.net/forum/init3-section-not-executed
uint8_t mcusr_mirror __attribute__ ((section (".noinit")));

void get_mcusr(void) __attribute__((naked, used, section(".init3")));
void get_mcusr(void)
{
    mcusr_mirror = MCUSR;
    MCUSR = 0;
    wdt_disable();
}


void setup()
{
    errm_create_callback = error_create_callback;

    gpio_conf(pin_EMERGENCY, OUTPUT, 0);  // active low

    // set up fan PWM
    gpio_conf(pin_FAN, OUTPUT, 1);
    // start with 50 % duty
    OCR2 = 128;
    // timer2 is also used by RPM.cpp
    // fast PWM, non-inverting (cannot use phase correct PWM because RPM.cpp
    // requires interrupt every 0.128 ms)
    TCCR2 = (1<<COM21) | (1<<WGM21) | (1<<WGM20);
    // clk / 8, every 0.128 ms (necessary for RPM.cpp)
    TCCR2 |= (1<<CS21);

    // Problems with fan PWM:
    // - OCR2=0 results in extremely short pulses, but the optocoupler eats them
    // - R2 on power board would need to be changed from 1M to 3k3
    // - fan starts @ OCR2=40, need to set minimum to 45

    // We don't use Arduino's yield, so _delay_ms should be OK (less flash space)
    _delay_ms(10);  // Vcc should be stable before EEPROM is written to.

    uart_init();
    settings_init();

    gpio_conf(pin_REL1, OUTPUT, 0);
    gpio_conf(pin_REL2, OUTPUT, 0);
    gpio_conf(pin_REL3, OUTPUT, 0);
    gpio_conf(pin_REL4, OUTPUT, 0);

    //gpio_conf(pin_FAN_extra, INPUT, NOPULLUP);
    //gpio_conf(pin_VSENSE, INPUT, NOPULLUP);
    //gpio_conf(pin_ACS712, INPUT, NOPULLUP);
    //gpio_conf(pin_ACS712_2, INPUT, NOPULLUP);
    //gpio_conf(pin_NTC1, INPUT, NOPULLUP);

    RPM_init();
    ADC_init();
    Hbridge_init();
    gpio_conf(pin_ENABLE, INPUT, PULLUP);

    if (mcusr_mirror & (1<<WDRF))
    {
        // reset command used
        if (eeprom_read_byte(EEPROM_RESET_ADDRESS) == EEPROM_RESET_VALUE) {
            // eeprom_write_byte would be faster, but I don't have enough flash
            // space for it.
            eeprom_update_byte(EEPROM_RESET_ADDRESS, 0);
        }
        // unexpected watchdog reset
        else errm_add(errm_create(&etemplate_WDT_reset, mcusr_mirror));
    }

    _delay_ms(100);

    wdt_enable(WDTO_1S);
    wdt_reset();
    // always report reset reason
    serial_puts_p(PSTR(">boot MCUSR: "));
    serial_putuint(mcusr_mirror);
    serial_puts_p(PSTR("\r\n"));
    serial_flush();
}


void loop()
{
    RPM_loop();
    ADC_loop();
    uart_loop();

    enabled.hardware = !gpio_rd8(PIN, pin_ENABLE);
    if (!is_enabled() && mode != mode_stopping && mode != mode_emergency)
    {
        set_mode(mode_stopping);
    }
    if (is_enabled() && mode == mode_stopping)
    {
        set_mode(mode_const_duty);
    }

    static unsigned long stopping_prev_ms = 0;
    unsigned long now = millis();
    switch (mode)
    {
        case mode_stopping:
            if (now - stopping_prev_ms >= stopping_period)
            {
                stopping_prev_ms = now;
                uint8_t tmp = stopping_duty + stopping_step;
                stopping_duty = (tmp > stopping_duty) ? tmp : 255;
                Hbridge_set_duty(stopping_duty);
            }
            if (now - mode_prev_millis >= stopping_time)
            {
                // TODO do this based on energy instead??
                if (RPM >= settings[kStoppingRPM].value)
                {
                    gpio_clr(pin_EMERGENCY);
                    // Failsafe - do not boil water in case the contactor is
                    // disconnected.
                    // Actually, that is not a good idea when stopping mode is
                    // also used for OVP.
                    //Hbridge_set_duty(0);
                }
            }
            break;

        default:
            break;
    }

    wdt_reset();
}

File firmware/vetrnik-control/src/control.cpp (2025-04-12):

#include "control.h"
#include "settings.h"
#include "power_board.h"
#include "lisp.h"
#include "debug.h"
#include "mqtt.h"
#include "pump.h"
#include "log.h"
#include <Arduino.h>

static control_strategy_t strategy = control_emergency;
static unsigned long contactor_prev_millis = 0;
static bool contactor_state = false;


void control_init()
{
    control_set_strategy(control_emergency);
}


/**
 * To be called when a new state object is received from power board.
 * Also called when state is invalidated after timeout.
 */
void control_new_state()
{
    if (!power_board_status.valid && strategy != control_emergency)
    {
        // If status becomes invalid, it means that communication with power
        // board was lost. This function isn't called before the first status
        // message is received, so no problems at startup.
        control_set_strategy(control_emergency);
    }

    switch (strategy)
    {
        case control_emergency:
            if (power_board_status.mode != pwrmode_emergency)
            {
                log_add_event_and_println(kControlNotEmergency, INFO);
                power_board_set_mode(pwrmode_emergency);
            }
            break;

        case control_MQTT:
            if (millis() - MQTT_last_command_ms >= 30000UL)
            {
                log_add_event_and_println(kControlMqttTimeout, INFO);
                control_set_strategy(control_emergency);
            }
            break;

        case control_lisp:
            {
                bool success = lisp_run_blind("(ctrl)");
                if (!success)
                {
                    log_add_event_and_println(kControlLispError, INFO);
                    control_set_strategy(control_emergency);
                }
            }
            break;

        case control_manual:
            break;
    }
}


void control_loop()
{
    const unsigned long now = millis();

    // control_contactor_set expiration
    if (now - contactor_prev_millis >= settings.contactor_debounce_min * 60000UL)
    {
        contactor_state = false;
    }

    // set contactor state
    digitalWrite(PIN_EMERGENCY, contactor_state && strategy != control_emergency);

    // Handle external e-stop button, hardware OVP, ...
    static bool prev_estop = false;
    static unsigned long estop_millis = 0;
    // this value will be true if something is wrong (emergency contactor is
    // in emergency state when it is not expected to.)
    bool estop = (
            control_get_strategy() != control_emergency &&
            power_board_status.mode != pwrmode_emergency &&
            power_board_status.mode != pwrmode_stopping && // stopping mode can sometimes use the emergency contactor
            contactor_state &&
            !digitalRead(PIN_CONTACTOR_SENSE)
        );

    // the contactor is slow, let's give it some time before actually tripping
    if (prev_estop && now - estop_millis >= 500UL)
    {
        log_add_event_and_println(kControlEstop, INFO);
        control_set_strategy(control_emergency);
    }

    if (estop && !prev_estop) estop_millis = now;
    prev_estop = estop;
}


void control_set_strategy(control_strategy_t s)
{
    log_add_record_control_strategy(strategy, s);
    INFO->print("Switching to ");
    INFO->println(control_strategies[s]);

    switch (s)
    {
        case control_emergency:
            power_board_set_duty(0);
            power_board_set_mode(pwrmode_emergency);
            power_board_set_software_enable(false);
            pump_set(false);
            contactor_state = false;
            digitalWrite(PIN_EMERGENCY, LOW);
            break;

        case control_manual:
        case control_MQTT:
        case control_lisp:
            // PIN_EMERGENCY should be controlled via control_contactor_set()
            //digitalWrite(PIN_EMERGENCY, HIGH);
            break;
    }
    strategy = s;
}


bool control_set_strategy(const char * str)
{
    for (size_t i = 0; control_strategies[i] != nullptr; i++)
    {
        if (strcmp(str, control_strategies[i]) == 0)
        {
            control_set_strategy((control_strategy_t)i);
            return true;
        }
    }
    return false;
}


control_strategy_t control_get_strategy()
{
    return strategy;
}


/**
 * Control contactor state
 *
 * Call when you want to connect the generator to the device.
 * If all other conditions are met (e.g. !emergency), the contactor
 * will operate and be kept that way until settings.contactor_debounce_min
 * minutes pass since the last call to this function.
 *
 * In normal operation, this function should be called repeatedly as
 * long as the turbine is spinning.
 */
void control_contactor_set()
{
    contactor_prev_millis = millis();
    contactor_state = true;
}


/**
 * Get state of contactor control
 *
 * This checks whether the contactor is told to be on, not whether it is
 * actually energized. It could still be off e.g. if this function says on but
 * we are in emergency mode.
 *
 * @return remaining time in ms if on, -1 otherwise
 */
unsigned long control_contactor_get()
{
    if (!contactor_state) return -1;
    unsigned long now = millis();
    return (settings.contactor_debounce_min*60000UL - (now - contactor_prev_millis));
}

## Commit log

2022-08-26 Temer kompletni anotovane schema
    [AVR-MCU.sch, H-bridge.sch, zvire-vetrnik-power.kicad_pcb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]
2022-08-27 Pred off-board soucastkami
    [zvire-vetrnik-power.kicad_pcb, zvire-vetrnik-power.sch]
2022-09-06 Vyrobena verze power PCB
    [AVR-MCU.sch, H-bridge.sch, zvire-vetrnik-power.kicad_pcb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]
2022-09-18 Fix behavior of enable pin
    [main.cpp]
2022-09-18 Add note to schematic
    [zvire-vetrnik-power.sch]
2022-09-19 Make strings shorter to save FLASH space
    [main.cpp]
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2022-09-24 Add filter cap for noise immunity in RPM circuit
    [AVR-MCU.sch]
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2022-10-07 Remove refresh requirement from power datapoint
    Sending m003 mulitple times is not a good idea.
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2023-01-20 Fix RX_datapoints ignoring $ and =
    [cli.cpp, uart_power.cpp]
2023-01-20 [power] Fix heatsink_temperature resolution
    [adc.cpp, settings.h]
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2023-01-22 [control] Fix CLI watch command buffer size
    [cli.cpp]
2023-01-22 [control] Print out stack trace on error
2023-01-24 [hardware] Add CAD designs for current sensor
    [zvire-vetrnik-current-sensor.kicad_pcb, zvire-vetrnik-current-sensor.sch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]
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2023-01-27 [control] Move settings from EEPROM to SPI flash
    EEPROM was emulated in internal FLASH...
2023-01-27 [control] Make address in SPIflash ls shorter
    [cli.cpp]
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2023-01-31 [power] Move RMS filter processing to ISR
    | conditions | before | after |
    |:--------------|:----------------|:----------------|
    | d128 with cap | 10.370A (1.030) | 10.065A (1.007) |
    | d128 w/o cap | 10.614A (0.936) | 10.065A (0.936) |
    | d255 with cap | 16.653A (1.671) | 16.592A (1.661) |
    | d255 w/o cap | 16.531A (1.651) | 16.470A (1.647) |
    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
2023-01-31 [power] Don't require datapoint refresh if shorted
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2023-02-03 [power] [HW] Fix connector label for SHORT
    [zvire-vetrnik-power.sch]
2023-02-03 [hardware] Add control board schematics
    [zvire-vetrnik-control.kicad_pcb, zvire-vetrnik-control.sch]
2023-02-04 [hardware] Design PCB for control board
    [zvire-vetrnik-control.kicad_pcb, zvire-vetrnik-control.sch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]
2023-02-04 [hardware] Design other PCBs
    [zvire-vetrnik-current-sensor-opamp.kicad_pcb, zvire-vetrnik-current-sensor-opamp.sch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]
2023-02-05 [hardware] Generate gcode for PCB milling
    [zvire-vetrnik-relays.kicad_pcb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]
2023-02-08 [hardware] Update PCB designs
    [zvire-vetrnik-control.kicad_pcb, zvire-vetrnik-power-supply.kicad_pcb]
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2023-02-08 [control] Beep buzzer at boot
    [main.cpp]
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2023-02-09 [control] Use PB1 as SPIflash SS instead of PB2
    [zvire-vetrnik-control.sch]
2023-02-09 [control] Improve error message in CLI
    [cli.cpp]
2023-02-09 [control] Use ethernet reset pin
    Mostly just to prevent issues with noise that might occur when it's left
    floating.
    Even touching the pin with a DMM probe would cause a reset.
    [main.cpp, settings.h]
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2023-02-09 [hardware] Resistor values in current-sensor-opamp
    [zvire-vetrnik-current-sensor-opamp.kicad_pcb, zvire-vetrnik-current-sensor-opamp.sch]
2023-02-10 Add current-sensor-opamp notes
    [440mV-10nF.csv, 440mV-33nF.csv, 440mV-noosc-33nF.csv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]
2023-02-11 [control] Fix use of uninitialised TelnetStream
    [cli.cpp]
2023-03-05 [power] Add extra NTC for rectifier heatsink
    [AVR-MCU.sch]
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2023-03-09 [control] Add CLI command to reset ethernet
    [cli.cpp, main.cpp, mqtt.cpp]
2023-03-09 [control] Automatically reset ETH if it gets stuck
    [mqtt.cpp]
2023-04-07 [hardware] [control] Fix Ethernet reset by EMI
    [zvire-vetrnik-control.sch]
2023-04-08 [control] Sense contactor state and handle e-stop
    [zvire-vetrnik-control.sch]
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2023-04-28 [power] Add uart command for resetting the MCU
2023-04-28 [power] Handle WDT reset as an errm error
    [main.cpp]
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2023-04-28 [power] Replace cli/sei with ATOMIC_FORCEON
    [Hbridge.cpp, adc.cpp]
2023-04-28 [power] Use avr/eeprom.h instead of Arduino EEPROM
    This saves about 192 bytes of FLASH space.
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2023-04-29 [power] Fix reset command
    [main.cpp, settings.h]
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2023-04-30 [power] Fix uart sending int instead of uint
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2023-06-16 [hardware] Add enclosure design
    [vetrnik-krabice.dxf]
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2023-07-17 [hardware] Add notes to control PCB design
    [zvire-vetrnik-control.kicad_pcb]
2023-07-17 [control] Fix MQTT DS18B20 ignoring force_report
    [mqtt.cpp]
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2023-07-24 [LISP] Fix error if t0 temperature is nil
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2023-07-25 [control] Fix MAKETMP_DECIMAL for uint32_t
    [mqtt.cpp]
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2023-08-16 [power] Set duty to 0 when stopping and shorted
    [main.cpp, settings.h]
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2023-08-16 [control] Fix Home Assistant power board commands
2023-09-01 [control] Reduce socket timeout for MQTT
    This should hopefully allow us to respond to the power board in time.
2023-09-01 Revert decreased MQTT timeout
    It kept going unavailable and back online several times a minute.
    [mqtt.cpp]
2023-09-05 [control] Log MQTT publish failures
    [mqtt.cpp]
2023-09-05 [control] Fix printf format strings
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2023-09-06 [control] Fix log printing bug
2023-09-06 [control] Fix pump log spam
2023-09-17 [control] Reduce socket timeout for MQTT
    1 second did not work, but 2 seconds might be just enough.
    [mqtt.cpp]
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2023-12-08 Rename hardware projects
    [440mV-10nF.csv, 440mV-33nF.csv, 440mV-noosc-33nF.csv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]
2023-12-08 Remove outdated gbrjob files
    [vetrnik-control-job.gbrjob, vetrnik-current-sensor-job.gbrjob, vetrnik-current-sensor-opamp-job.gbrjob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]
2023-12-08 Rename enclosure documentation
    [vetrnik-enclosure.dxf]
2023-12-08 Migrate KiCAD projects to KiCAD 7.0
    [AVR-MCU.kicad_sch, AVR-MCU.sch, H-bridge.kicad_sch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]
2023-12-08 [control] Fix unused variable in uart_power.cpp
    [uart_power.cpp]
2023-12-22 [control] Fix printing of MQTT publish error log
2023-12-22 [control] Log software reset event
    This should help with analyzing the log timestamps.
    [cli.cpp]
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2023-12-22 [control] Prevent immediate MQTT reconnect
    [mqtt.cpp, settings.h]
2023-12-22 [control] Log last millis value before reset
    [main.cpp]
2024-03-13 [hardware] Add designs of vetrnik-H-bridge
    [TO-247-scale.dxf, vetrnik-H-bridge.kicad_pcb, vetrnik-H-bridge.kicad_sch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]
2024-03-23 [control] Make reset cause name shorter
    The kReboot message wouldn't fit in 80-character buffer in log.cpp
    [reset_cause.cpp]
2024-03-24 [hardware] Exclude vetrnik-H-bridge parts from BOM
    [vetrnik-H-bridge.kicad_pcb, vetrnik-H-bridge.kicad_sch]
2024-03-31 [hardware] Add info about hardware mods
    [AVR-MCU.kicad_sch, H-bridge.kicad_sch, OVP-hysteresis.ods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]
2024-04-10 [hardwa] Add info about hardware mods
    [vetrnik-control.kicad_sch]
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2024-06-23 [control] Make reset cause names shorter
    This should help avoid "\r\n" not fitting in print_buffer in kReboot log
    message.
    [reset_cause.cpp]
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2024-06-26 [control] Fix bug in settings print
2024-06-26 [control] Do not scroll past error messages in cli
    [cli.cpp]
2024-06-26 [power] Fix new cppcheck warnings
    [Hbridge.cpp]
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2024-06-27 [power] Report reset reason on boot
    [main.cpp]
2024-06-27 [power] Add setting for min duty cycle
    This should prevent random resets occurring @ low duty cycles.
    [Hbridge.cpp, settings.h]
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2024-06-27 [control] Try to fix WDT reset on mqtt reinit
    [mqtt.cpp]
2024-06-27 [control] Fix cat sometimes drops start of line
    [cli.cpp]
2024-06-27 [control] Fix e-stop detection too fast
    The contactor takes a long time to turn off
    [control.cpp]
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2024-06-27 [power] Fix PWM generation
    [adc.cpp, main.cpp]
2024-06-27 [hardware] Add info about vetrnik-power fan mod
    [vetrnik-power.kicad_sch]
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2024-06-30 [control] Fix MQTT bugs
    It would get stuck in eth_skip
    [cli.cpp, mqtt.cpp, settings.h]
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2024-08-23 [hardware] Add measurement data
    [d10-wav1.csv, d10-wav2.csv, d100-wav1.csv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]
2025-02-01 [hardware] Add vetrnik-wind-sensor
    [vetrnik-wind-sensor.kicad_pcb, vetrnik-wind-sensor.kicad_sch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]
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2025-02-21 Prevent watchdog reset after MQTT_reinit
    No idea if this will actually help.
    [mqtt.cpp]
2025-02-21 Improve MQTT_reinit watchdog fix
    [mqtt.cpp]
2025-02-21 Add missing wind sensor disable logic
    [sensor_wind.cpp]
2025-02-21 Fix missing pinMode in sensor_wind
    [sensor_wind.cpp]
2025-02-21 Fix wind sensor state machine
    [sensor_wind.cpp]
2025-02-21 Fix flood of MQTT msgs on wind sensor disconnect
    [mqtt.cpp]
2025-02-22 Add missing header include to reset_cause
    This will prevent the build from failing when ststm32 is updated.
    ststm32@15.6.0
    RAM: [======== ] 81.5% (used 53396 bytes from 65536 bytes)
    Flash: [===== ] 49.6% (used 129944 bytes from 262144 bytes)
    ststm32@16.0.0
    RAM: [======== ] 81.5% (used 53396 bytes from 65536 bytes)
    Flash: [===== ] 51.3% (used 134608 bytes from 262144 bytes)
    ststm32@17.0.0
    RAM: [======== ] 82.9% (used 54328 bytes from 65536 bytes)
    Flash: [===== ] 51.7% (used 135576 bytes from 262144 bytes)
    ststm32@17.3.0
    RAM: [======== ] 82.8% (used 54252 bytes from 65536 bytes)
    Flash: [===== ] 51.1% (used 133916 bytes from 262144 bytes)
    ststm32@17.4.0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
    [reset_cause.cpp]
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2025-02-23 [power] Fix 'make puncover'
2025-02-23 [power] Fix stopping mode duty overwritten by uart
    [main.cpp]
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2025-02-28 Improve block diagram
    Add missing capacitor;
    Add arrows heads to measurement lines
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2025-04-12 Rename PIN_SHORT to PIN_EMERGENCY
    The contactor no longer shorts the wind turbine output on this hardware
    revision.
    [hardware.h, main.cpp]
2025-04-12 Rename etemplate_OVP_stop to _emergency
    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
    [adc.cpp]
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2025-04-12 Fix power board mode comments
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2025-04-12 [control] s/control_shorted/control_emergency/
    The contactor no longer shorts the turbine, it disconnects it.
    [control.cpp, mqtt.cpp]
2025-04-12 [control] Remove mentions of shorting the generator
    [control.cpp]
2025-04-18 [lisp] Add adaptive HCS MPPT
    [vwind-ramps.csv]
2025-04-19 Revert to inline MQTT command handlers
    before:
    RAM: [======== ] 81.5% (used 53412 bytes from 65536 bytes)
    Flash: [===== ] 50.5% (used 132340 bytes from 262144 bytes)
    after:
    RAM: [======== ] 81.5% (used 53412 bytes from 65536 bytes)
    Flash: [===== ] 50.5% (used 132268 bytes from 262144 bytes)
    This saves 72 bytes
    [mqtt.cpp]
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2025-04-20 [model] Add TSR-PI to controller comparison
    [vwind-ramps.csv]
2025-04-21 [lisp] Improve controller comparison data
    Best results were achieved with:
    Ts = 12.0
    SA = 3
    Ts = 8.0 for HCS-adaptive
    [vwind-ramps.csv]
2025-04-28 [control] Fix MQTT commands
    [mqtt.cpp]
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2025-05-01 [hardware] Clean up vetrnik-H-bridge schematic
    [vetrnik-H-bridge.kicad_pcb, vetrnik-H-bridge.kicad_sch]
2025-05-01 [hardware] Clean up vetrnik-power schematic
    [AVR-MCU.kicad_sch, H-bridge.kicad_sch, vetrnik-power.kicad_pcb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]
2025-05-01 [hardware] Clean up vetrnik-current-sensor-opamp
    [vetrnik-current-sensor-opamp.kicad_pcb, vetrnik-current-sensor-opamp.kicad_sch]
2025-05-01 [hardware] Clean up vetrnik-power-supply
    [vetrnik-power-supply.kicad_pcb, vetrnik-power-supply.kicad_sch]
2025-05-01 [hardware] Clean up vetrnik-relays
    [vetrnik-relays.kicad_pcb, vetrnik-relays.kicad_sch]
2025-05-01 [hardware] Clean up vetrnik-wind-sensor
    [vetrnik-wind-sensor.kicad_sch]
2025-05-01 [hardware] Clean up vetrnik-control
    [vetrnik-control.kicad_pcb, vetrnik-control.kicad_sch]
